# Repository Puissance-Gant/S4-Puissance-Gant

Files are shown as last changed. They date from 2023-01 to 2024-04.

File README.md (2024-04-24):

# S4-Puissance-Gant

Voici le répertoire du projet de session de l'équipe Puissance Gant :gloves::robot:

## Membres
<pre>
- Comtois, Ludovic    (coml1502)
- Corduneanu, Andrei  (cora5428)
- Delev, Milan        (delm1301)
- Den Hartog, Daniel  (deno2501)
- Martin, Frédérick   (marf0702)
- Theoret, Marek      (them0901)
</pre>

## Objectif du projet
L'équipe Puissance Gant avait pour but de concevoir une main robotisée ainsi qu'un système de contrôle à distance intuitif. Le produit final consiste en une main à trois doigts indépendemment contrôlés par un gant auquel des potentiomètres coulissants ont été attaché. Une interface utilisateur permet d'observer l'état du robot et de le contrôler manuellement.

### Le projet en action
cliquez sur l'image:<br><br>
[](https://youtu.be/RtNsFn4x6qA)

## Fonctionnement global
Le fonctionnement spécifique de chaque composante est décrite dans leur sous-dossier respectif.

Il y a trois composantes principales qui communiquent entre elles à l'aide d'un serveur de communication sans-fil par WI-FI. L'état du gant est lu par une carte ESP32 qui envoie la position des doigts au système. Un ordinateur reçoit ces informations et les transmet à une carte OpenCR qui contrôle les moteurs de la main. Un deuxième ordinateur affiche une interface utilisateur qui permet d'afficher des informations utiles et de contrôler la main manuellement.

### Performance
La latence globale du contrôle, donc entre le mouvement de la main de l'utilisateur et le mouvement de la main est d'environ 200ms et est plutôt constant. La main peut d'ailleurs tenir une banane de 200g sans la faire tomber.

### Pistes d'amélioration
<pre>
- Changer la forme de la main robotisée et l'emplacement des doigts afin d'optimiser la prise d'objets. 
- Utiliser un meilleur système de tension pour la prise d'objets, qui empêcherait les doigts de bouger lors de la prise d'objets.
- Changer la carte OpenCR pour une carte qui peut se connecter au WI-FI. (Par exemple, un ESP32 et une carte-soeur de contrôle des moteurs)
- Rendre le serveur accessible sur tous les réseaux. Les appareils doivent actuellement être sur le même réseau WI-FI que le serveur pour s'y connecter.
- Changer le système d'acquisition de données du gant. Par exemple, un exosquelette. (Faire attention aux résistances flexibles, elles sont souvent peu fiables.)
</pre>

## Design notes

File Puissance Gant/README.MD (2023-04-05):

# Organisation des dossiers
Les dossiers sont organisés tel que l'assemblage physique de la main et du gant sont dans un dossier séparé de la programmation qui leur est associé.

Les sous-dossiers de programmation indiquent comment utiliser le code, quelles librairies installer et sur quel appareil installer quel code.

Les sous-dossiers de mécanique et d'électrique indiquent comment assembler le gant et la main et quel matériel a été utilisé.

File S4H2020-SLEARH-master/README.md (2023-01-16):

# Project-SLIRUS
Articulated robotic hand designed for sign language interpretation
Continuation from the SLEARH project: https://github.com/UdeS-GRO/S4H2020-SLEARH

# Preriquisites:
Hardware:
  - Open CR;
  - 1 usb to micro usb;
  - 1 drive for the motors ( (PCA-96 85) link: https://www.sunfounder.com/pca9685-16-channel-12-bit-pwm-servo-driver.html);
  - 12 electrical step motors ((Smraza 9G Micro Servo Motor) link: https://www.amazon.ca/gp/product/B0886351PP/ref=ppx_yo_dt_b_asin_title_o00_s00?ie=UTF8&psc=1);
  - RaspberryPi 3B+;
  - Micro-SD card (for RPi image);
  - 2 Dynamixel XL-430;
  - A voltage source with a current limit of more than 2 A;
  - 12 V power source, to 5.1mm center positive barrel jack;
  - Piece of plywood 30cm by 30cm (optional, but recommended);
  
Software;
  - Python 3.7(installed for this gitProject, but not necessarily needed);
  - Python Library:
    - pySerial;
    - tkinter;
  - Arduino IDE for the compiler;
  - Arduino Library:
    - Adafruit_PWMServoDriver.h;
    - ArduinoJson.h;
    - Wire.h;
    (But they all should be downloaded with the plateformio.ini)
  -Qt (5.7.1 or newer)
    
# Steps to start your project:
  - Read the Mechanics/README.md for informations on how to build the hand;
  - Read the Electrics/README.md for informations on how to plug the motors and the drive on the arduino;
  - Read the Interface/README.md for informations on how to use the interface
  - Read the Speech_to_text/README.md for informations on how to install the necessary librairies for the speech-to-text and create a key for the API connection
  - Install your favorite python IDE;
  - Open this git repo in a new project and create a python RunTool for UI_Main_Script.py script (that's where the application starts);
  - Install pySerial on your computer (it will appears in your python <python path>/Lib/*);
  (Now, your python side of the project should be up to run)
  - Install VsCode on your computer;
  - Install plateformio and ArduinoIDE in your vscode;
  - Set your Arduino_debug.exe path in your VsCode setups;
  - Build the project one first time (and it should load all the needed libraries);
  (Now, your Arduino side of the project should be up to run)
  - Import OpenCr library as shown in this video: https://www.youtube.com/watch?v=dQw4w9WgXcQ
  - Plug the Arduino to your computer and start the UI_Main_Script.py to start the application and the Arduino thread!
  
 # Steps to be able to run to application on the Raspberry Pi 3b+
  - Flash your Micro-SD card with an up to date RPi image running a linux operating system (you can flash your Micro-SD card with this       tool: https://www.balena.io/etcher/);
  - Connect your Micro-SD card in your RPi and open it with an internet cable or via VMWare for example;
  - On the first RPi's run, set your preferences;
  - Now, open a terminal and instal python 3.6 (or niewer, this could take some time) (this link could be usefull: https://github.com/instabot-py/instabot.py/wiki/Installing-Python-3.7-on-Raspberry-Pi);
  - Install the PySerial library with:
    $ sudo apt-get install pyserial
  - If you're connected to your RPi via VMWare or ssh, run this command:
    - $ export DISPLAY=:0
  - Create your project directory where you want it on your RPi:
    - $ cd "DIRECTORY PATH"
    - $ mkdir "PROJECT NAME"
    - $ cd "PROJECT NAME"
    - $ git clone "THE PROJECT'S LINK"
    - $ git pull
  - The project should now be copied locally onto your RPi;
  
  - Now go to the project's Ui_Main_script.py path on your RPi and run the program through a terminal:
    - $ python Ui_Main_Script.py
  
# Now Have Fun !

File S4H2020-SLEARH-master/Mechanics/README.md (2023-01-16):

ASSEMBLY OF THE HAND

1. Start by opening the BOM file in this folder.
2. With a 3D printer at 40% fill and supports, print all the parts that have &quot;3D printed&quot; as a link. Some parts need to be printed more than once, refer to the quantity column of the BOM to know how many.
3. Cut all the pivot rods with lenghts and quantity as described in the BOM (index 15-16)
4. Separate all the printed parts for each of the fingers where each number is the index in the BOM;

Pinky: 2 – 6 – 4 – 5

Ring finger: 2 – 6 – 4 – 5

Middle finger: 1 – 6 – 4 – 5

Index finger: 1 – 6 – 4 – 5 - 13 - 10 - 18

Thumb: 3 – 6 – 8 – 10 – 9 - 12

The assembly of the fingers is done with rods that are used as pivots in the joints. The servos' moving lever are fixed on the 3D printed levers with nails. The nail's head holds the lever in place and the other end is press fitted into the 3d printed lever.

Assembly of the pinky finger:
1. Attach part 2 and 6 with a 14mm pin. The assembly should be able to move freely.
2. Attach part 2 and 4 together with a 14mm pin.
3. Screw a Servo on part 6.
4. Attach part 5 and 6 with a 14mm pin.
5. With a nail, attach part 4 to the servo screwed on part 6.
6. Screw a servo on part 7.
7. With a nail, attach part 5 to the servo screwed on part 7.

For the four other fingers follow the same steps as for the pinky finger using the parts specified earlier.

When the fingers are assembled, the servo holders are cliped on the palm and a rod is inserted in the pivot.

Assembly of the base:
8. Install the motors drive on the back of the hand with the four bolts of index 29.
9. Make all the electric connections relating to the hand motors as explained in the electric README.
10. Insert a rod of index 26 into the forearm (index 20) until the exposed part of the rod is roughly the same length as the thickness of the base.
11. With the bolts of index 28, install the Open CR and the raspberry pi on the forearm.
12. Insert one of the Dynamixel in the cage located on the forearm until the rotating circle is level with the exterior of the cage.
13. Fasten the 3D printed piece of index 23 to the Dynamixel installed in step 24 using 2 bolts of index 27.
14. Insert the other Dynamixel in the rectangular enclosure in the base, and fasten the gear of index 21 to said Dynamixel using 2 bolts of index 27.
15. Insert 2 bearings of index 22 in the circular grooves in the base.
16. Place the protruding rod of the forearm into the hols in the base, making sure that the gear installed in step 26 and the gear of the forearm mesh together.
17. Connect the hand to the forearm using a rod of index 25, making sure that the driver side of the palm faces the Dynamixel in the forearm.
18. Install the wrist lever arm (index 24) between the forearm dynamixel and the protruding hole at the bottom of the palm.
19. Connect the Dynamixels as explained in the electric README.
If desired, you can screw a wooden platform to the base for added stability.

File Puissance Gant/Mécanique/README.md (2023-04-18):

# GUIDE D'ASSEMBLAGE DE LA MAIN ET DE L'AVANT BRAS

1. La main est une pièce unique fait a l'aide de solidworks, comme toutes les autres.



2. Afin de joindre les 14 pièces différentes, bien identifié dans le dossier, qui servent de doigts, il faut prendre un élastique coupé et le mettre de manière à ce que chaque bout de l'élastique passe dans un des deux trous arrières de la pièce. Une fois les trois pièces de doigts assemblées (deux pour le pouce) il faut passer l'élastique dans les deux trous arrière du haut de la main prévu pour chaque doigt. (1 à 2 élastiques par doigts) 




3. Avant d'attacher l'élastique il faut que celui-ci soit tendu le plus possible sans qu'il ne fend.

4. Deux vis(Ø~0.5cm,longueur>3.5cm), quatres rondelles et deux écrous permettent de connecter la main et l'avant-bras

5. Les trois moteurs ROBOTIS Dynamixel X-Series XL430-W250 sont placés à l'avant de l'avant-bras en positionnant le rotor de chaque moteur coïncidement avec les extrusions dans l'avant-bras prévu à cet effet. Ces moteurs sont fixés à l'avant-bras à l'aide de 8 vis pour chacun des moteurs. Les vis sont celles fournies dans le kit des moteurs.

6. Une poulie est fixé sur chacun de ces moteurs à l'aide de 2 vis, celles du kit. Un fil de pêche est attaché sur chacune des poulies en le passant tout d'abord par le trou au milieu des poulies les traversant. Cela permet de s'assurer que le noeud sur la poulie ne bougera pas. Ensuite, passer le fil dans les trous avant repectifs de l'avant-bras et de la main puis ensuite des doigts (pas le majeur et le petit doigts), jusqu'à le joindre au bout de chaque doigt à l'aide de l'élastique.



8. Le majeur, l'annulaire et le petit doigt sont relié entre eux par des bouts de bois collés avec de la colle chaude sur le derrière des phalanges. (2 morceaux, 1 en bas / 1 en haut, sur la phalanges du bas et 1 morceaux au milieu des deux autres phalanges)

9. Le moteur ROBOTIS Dynamixel X-Series XM430-W350 est installé sur l'arrière de l'avant-bras de la même manière que les trois XL430.

10. La pièce Mécanisme_Poignet_1 est attaché sur le moteur XM430 de la même manière que les poulies sur les autres moteurs.

11. La pièce Mécanisme_Poignet_2 est collé au milieu du derrière de la main ainsi qu'au Mécanisme_Poignet_1 avec de la colle chaude.

# Amélioration possible 

1. L'avant bras pourrait permettre d'accueillir deux moteurs de plus afin de contrôler individuellement chaque doigt.

2. Le pouce pourrait avoir une troisième phalanges et être repositionné pour lui permettre un mouvement plus utile lors de la prise d'objet.

3. La main pourrait être fait de manière plus concave afin de mieux reproduire sa forme réelle.

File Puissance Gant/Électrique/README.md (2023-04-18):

### Mécanique du gant
diag_mec

Description du montage:
- Chaque curseur de potentiomètre est attaché à un ressort le retenant à sa position zéro, soit vers l'arrière (vers le poignet).
- Chaque curseur est ensuite tiré par un câble, chacun parcourant au moins trois corridors d'alignement:
  - Au moins un corridor est placé sur le boitier, servant de premier point d'appui au câble pour ensuite se diriger vers le doigt assigné.
  - Au moins deux corridors sont placés sur chacun des doigts à mesurer et chacun est fixé sur un bague que l'utilisateur doit porter.
  - Les corridors sur les bagues distales servent de point d'ancrage au câble.
  - Plus de corridors peuvent être installés afin de maximiser la linéarité de la translation axiale du câble.
- En fléchissant les doigts, le câble est tiré, faisant varier la position du curseur du potentiomètre.
- Les ressorts doivent être suffisamment forts pour retenir les doigts au repos en position ouverte.

### Électronique du gant
diag_elec

Description du montage:
La mesure de la position des doigts se fait par la lecture des diviseurs de tension de chaque doigt
- Une résistance fixe est placée en série à un potentiomètre. Ici, 10 k et 100 k ohms respectivement.
- On applique la tension (Vcc; 3,3 V) à la résistance fixe et on branche le point du curseur à la masse (GND)
- La borne extrême du potentiomètre (résistance totale fixe) peut ne pas être branchée, cependant:
  - En fonction du modèle de potentiomètre, il est possible de placer la résistance fixe entre les bornes non-variables pour concevoir le diviseur de  tension, rendant le montage plus compact.
  - Dans le cas décrit ci-haut, la résistance fixe doit être de 11k afin d'équivaloir, avec la 100 k du potentiomètre, à 10 k ohms (circuit parallèle).
- La borne Vout (point de lecture) est entre la résistance fixe et le potentiomètre.
- La borne Vout de chaque diviseur de tension est branchée directement en input au ESP32D aux points GPIO 36, 39 et 34 pour le pouce, l'index et le majeur respectivement.
- Les points du ESP32D peuvent varier en fonction de votre programme.

### Photos de montage complété
Bien que rudimentaire, le montage illustré ci-contre sert de référence pour l'assemblage. À noter que les tiges des curseurs traversent le plafond du boitier dans une fente de la langueur du parcours du curseur et que les poteniomètres sont boulonnés par le haut.
gant_montage02

gant_montage01

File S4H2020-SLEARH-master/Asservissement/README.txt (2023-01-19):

Motors control

This README will explain how to control the different motors on the hand.
In the document Test_main, you can find all the three files needed for the motor control.

Test_main.ino
•	This file is the main. 
•	This is where we initialize all the motors (servomotors and dynamixels). When started, the hand stands up at is initial position and wait for a message from the interface.
•	The main uses the class COM_Arduino in the file Communication.h for all the function connected to the communication with the interface.
•	When a message is received from the interface, the functions from class Servo of the file controlServo.h are called to execute a letter.

controlServo.h
•	This file contains the class Servo.
•	The class Servo contains the struct Servo and all the function used in for the control of the motors.
•	The struct Servo contains all the configurations of the 5 fingers, the wrist and the base for all the characters (letters and numbers).
•	The three functions called form the main (Test_main.ino) are the setupBase, servoOut and the reverseMove.
•	The function setupBase is used to move the base and wrist at its initial position depended on is initial position.
•	The function servoOut is use the move all motors in the configuration of a specific letter or number.
•	The function reverseMove is use to replace the hand in is initial position.

Communication.h
•	This file contains the class COM_Arduino.
•	The class COM_Arduino contains all the function use to communicate with the interface.
•	The functions SendMessage and ReadMessage interact with the interface.
•	The functions Set_state and Get_state are useful if you want to manage the state of the object.

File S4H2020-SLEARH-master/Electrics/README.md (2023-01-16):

# Electrical Parts list

    Name	              Description	                                Quantity
    ------------------------------------------------------------------------
    Open CR     	      OpenCR1.0     	                              1
    Servo driver	      PCA9685 16 channel PWM servo Driver	         1
    Servo motors	      SG90 servo motor	                              12

# Electrical Connections:

  # OpenCR pins to Drive Pins
    - 5V   ------->    VCC
    - Ground  ---->    Ground
    - scl(pin15) ->    scl
    - sda(pin14) ->    sda
    
  # Drive pins to Servo Motors    
    - 0      --------> motor 0 (thumb bottom)
    - 1      --------> motor 1 (thumb top)
    - 2      --------> motor 2 (index bottom)
    - 3      --------> motor 3 (index top)
    - 4      --------> motor 4 (middle bottom)
    - 5      --------> motor 5 (middle top)
    - 6      --------> motor 6 (ring bottom)
    - 7      --------> motor 7 (ring top)
    - 8      --------> motor 8 (pinky bottom)
    - 9      --------> motor 9 (pinky top)
    - 10     --------> motor 10 (index base) 
    - 13     --------> motor 11 (thumb base) 

The 2A voltage source must be connected to the 2 pin terminal block of the drive.
The voltage source with the barrel jack must be connected to the female adapter on the OpenCR.
The 2 Dynamixel servos can be plugged into any of the TTL ports on the OpenCR.

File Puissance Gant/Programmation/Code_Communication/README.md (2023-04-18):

# Architecture de la communication
Le projet Puissance Gant utilise les protocoles MQTT et sériel pour faire communiquer les divers éléments. Le schéma suivant illustre les divers liens entre les contrôleurs et ordinateurs ainsi que les protocoles utilisés.
architecture_comm_2 drawio

# Communication sans-fil par MQTT
Cette section contient le processus pour l'installation et la configuration d'un serveur MQTT. MQTT est un protocole de communication sans fil utilisé dans les situation oû la bande passante est peu fiable ou faible. Le protocole MQTT utilisé est Eclipse Mosquitto. Il recommender d'installer le mqtt explorer afin de vérifier l'état du serveur. 

http://mqtt-explorer.com/

## Installation du serveur sur le raspberry pi

Afin d'installer le serveur sur le raspberry pi, il faut tout d'abord intaller un système d'operation. Le système d'operation recommandé est ubuntu server 22.10. 

https://ubuntu.com/download/server

Par la suite, il faut installer un serveur MQTT sur le raspberry pi. Pour l'installation, il est recommendé de suivre le tutoriel suivant: 

https://diyi0t.com/microcontroller-to-raspberry-pi-wifi-mqtt-communication/

Il d'ailleurs utile d'installer *MQTT Explorer*, qui est une application qui permet de visualiser et de gérer les messages en temps réel. Celà facilite le débogage et le développement d'applications MQTT.

http://mqtt-explorer.com/

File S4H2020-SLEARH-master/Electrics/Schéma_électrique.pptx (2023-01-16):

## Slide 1

PCA9685
16 CHANNEL 12-BIT PWM
I2C ADDRESS I[A5..A0][R/W]
VDD : 2.3-5.5V IO : 5V SAFE
OUTPUT : 25mA EACH/400mA TOTAL

GND PWM0
SDA PWM1
SCL PWM2
VCC PWM3
PWM4
PWM5
PWM6
PWM7
PWM8
PWM9
PWM10
PWM11
PWM12
PWM13
PWM14
PWM15

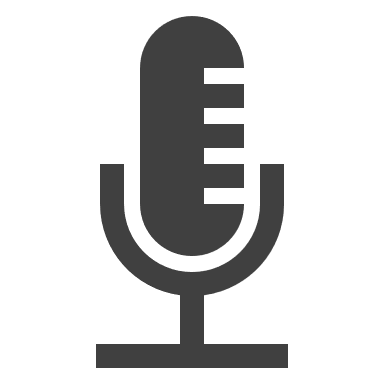
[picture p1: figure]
Micro de radio avec un remplissage uni

RASPBERRY PI

USB
USB
MICRO USB

OPENCR

GND
MICRO USB SDA
SCL
5V

POWER
SMPS IN

SERVO SG90-1
SERVO SG90-2
SERVO SG90-3
SERVO SG90-4
SERVO SG90-5
SERVO SG90-6
SERVO SG90-7
SERVO SG90-8
SERVO SG90-9
SERVO SG90-10
SERVO SG90-11
SERVO SG90-12

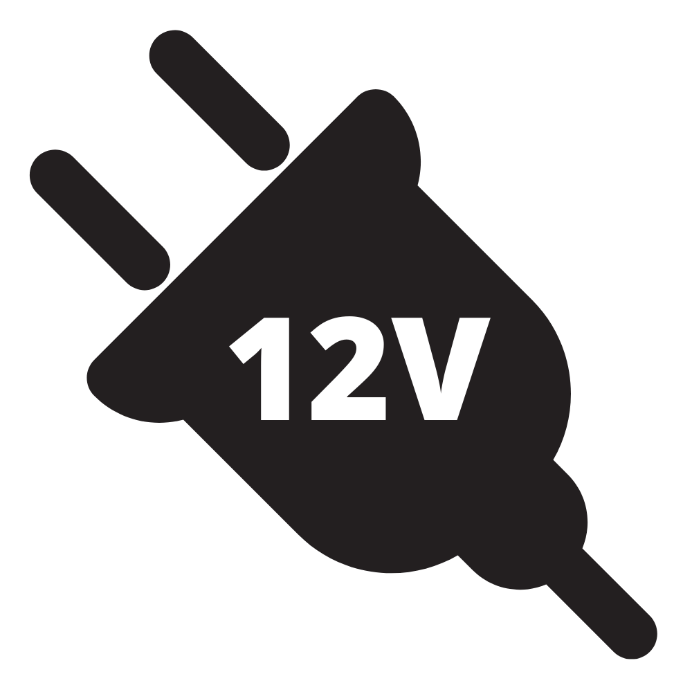
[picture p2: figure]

5V

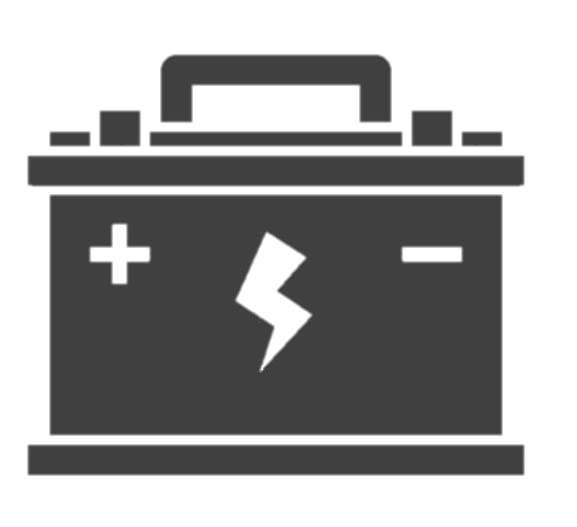
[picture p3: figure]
Car battery icon | Battery icon, Car battery, Car battery hacks

5V

AUXILIARY POWER
V+
GND

GND EXTCLK WHEN NOT IN USE

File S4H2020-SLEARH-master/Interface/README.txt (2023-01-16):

User interface:

The software used for the user interface was Qt 5.10. Be sure it is already installed before beginning the project
The program is ready to be used directly when you open it. However, some paths to other files (Enregistrement.py and 
FinPort.py) are implemented for our project. Make sure that these paths are modified for your files.
Furthermore, some aspects of the insterface can be used without the OpenCr (Speech-to-text and show characters), but the
transcription need the OpenCr to work well. 

Interface properties:
-The line edit on the top left changes the recording time of the speech-to-text. A recording time negative or 0 will trigger
an error message. Decimals have not been managed. The program only works if an integer is written. 
-The "Start record button" creates a process that runs the Enregistrement.py file. A label will appear when the program is ready 
to receive sound. Another label will appear when the recording is finished.
-After recording your phrase, it will appear underneath the Recording button.
-On the bottom left is the Start traduction button. It can only be used if a phrase has been recorded with the Speech-to-text property.
-On the bottom right, you can write a character to see the sign assciated with it. You can also write "all" to see every character
at the same time.
-On the top right, the big blank space will show the images of the characters.
-The last line edit on the bottom right near the middle is used for tests. You can write one or multiple characters and press enter 
to start the hand traduction. This way, you don't need to use the speech-to-text if you only want to test on or few letters.

When the traduction is started, the hand will show every character one by one. At the same time, the interface will show the character
the hand is doing. 

FindPort:
Communication between interface and OpenCr.

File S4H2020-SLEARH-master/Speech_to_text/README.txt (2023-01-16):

%%%%% This file will explain how to run the speech-to-text API on a Raspberry pi 3b+
 %%%%%

1. Creat_VenV.py

If you want to run you program in a virtual environment, you`ll need to create one. 
This file lets you chose the path and the name of your virtual environment.
ATTENTION: This file will not work on Windows or Mac, because the file writes directly in the command window available only in Linux

It is recommended to create a virtual environment if you have multiple python programs and they use different versions of modules/Packages. By creating a virtual environment, you can isolate the necessary 
packages and run them with the right program. An old library version is used in this folder, so a virtual envrionment may be helpful.

2. Install librairies

Libraries installations are quite simple with the right tools. First of all, be sure to install pip on your Raspberry pi

2.1  Activate virtual environment

If you have decided to create a virtual environment, you need to activate it to install the required packages

	2.1.1 - Open the command window (Habitually a black box on the top left)
	2.1.2 - write: "source /path/to/venv/bin/activate"
	2.1.3 - The virtual environment name should be written in the command window

You are now ready to install libraries in the virtual environment

2.2 Install librairies for the project

	2.2.1 - Open the command window
	2.2.2 - Write "python3 -m pip install package" where the "package" in the project is: soundfile, sounddevice, google-cloud-storage and google-cloud-speech

ATTENTION: We used the version 2.0.0 for the google-cloud-speech library. The RecognitionAudio and RecognitionConfig have then been modified

	2.2.3 - With these packages, the program may not work. At the moment of the project's creation, there are numpy and PortAudio problems with sounddevice and the Raspberry pi OS. 
	   You will then need to install a few more packages if it is your case.
	   Open the command window and write: "sudo apt-get install " and then install these libraries: libportaudio2, libasound-dev and libatlas-base-dev

3. Connection to API

In the file Enregistrement.py, a key is necessary to be able to use the Speech-to-text API.
When you create your own google-cloud account, you need to be able to get the key.
The key should be a json file and must be in the same folder as Enregsitrement.py when it is running or you need to write the full path to the key.

Step by step on how to setup the google cloud project for SLIRUS:
3.1-Create a google cloud project:
	3.1.1 - Create a google account(gmail) if you don't already have one. Be sure to put in a billing methode with the account. 
	3.1.2 - Go to the url--> https://console.cloud.google.com/
	3.1.3 - Click on the 3 dash bars on the top left of the screen.
	3.1.4 - Put your mouse on "Home" and click on "Dashboard".
	3.1.5 - Click on "New projet" and fillout the missing information.
3.2-Enable the Speech to text API for the project:
	3.2.1 - Click on the 3 dash bars on the top left of the screen.
	3.2.2 - Click on "APIs & Services".
	3.2.3 - Click on "ENABLE APIS AND SERVICES" at the top of the page.
	3.2.4 - Put "Cloud Speech-to-Text API" in the search bar and press Enter.
	3.2.5 - Click on the API "Cloud Speech-to-Text API".
	3.2.6 - Click on "ENABLE".
3.3-Get your JSON key:
	3.3.1 - Go back to "APIs & Services" and click on "Credentials".
	3.3.2 - Click on "Create Credential" and choose "Servive account".
	3.3.3 - In the menu click on "IAM & Admin" then on "Service Accounts".
	3.3.4 - Click on your service account and go to "KEYS".
	3.3.5 - Click on "ADD KEY" and choose JSON.

Now you should have the JSON key downloaded. This will allow you to have access to the APIs that were enable for your projet. 

4. Create a bucket in your google cloud project:
	4.1-Click on "Storage" in the menu. 
	4.2-Click on "CREATE BUCKET" and fill in the information required.
Remember the name of your bucket because you'll need to put it in the code ...

5. Run Enregistrement.py in the virtual environment

This section is reserved to those who use a virtual environment. 
To open the file in the virtual environment (and use the libraries inside), be sure that the virtual environment is still active.
Then, write in the command window "cd /path/to/file"
You should now be in the folder with the right files
Write in the command window "python3 Enregistrement.py" 
  
You should now be able to transcribe your voice into text.

6. Run Enregistrement_automatic_tests
This program lets you test your speech-to-text
Some words/sentences are already written in french. If you want to test in another language, you juste need to change them for what you want.
The recording time is set to 5 sec, but you can change it to whatever you want in the line calling the function
To make it work, speak clearly and a constant pace. 
Don't try too difficult phrases, because the API sometimes does little ortograph mistakes (For example "it eat")

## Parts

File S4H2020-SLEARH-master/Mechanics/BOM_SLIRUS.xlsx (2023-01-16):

Index | Part name | Qty | 3DPrinted | Description
1 | Phalange_Index-MiddleFinger | 2 | x | Index and middle finger end
2 | Phalange_RingFinger-PinkyFinger | 2 | x | Ring and Pinky finger end
3 | Phalange_thumb | 1 | x | Thumb finger end
4 | Finger_lever_distal | 4 | x | Lever for the four finger ends (except thumb)
5 | finger_lever_proximal | 4 | x | Finger lever that links fingers to the palm
6 | SG-90 Servo Socket | 5 | x | Servo Holder (part of the fingers)
7 | Servo Holder | 4 | x | Fix servo on the palm
8 | Thumb_Finger_lever_distal | 1 | x | Finger lever to move thumb end
9 | Proximal_thumb_lever | 1 | x | Lever to move thumb second part
10 | SG90 - Servo Socket_thumb | 1 | x | Servo socket (part ofthe thumb)
11 | Servo_holder_index | 1 | x | Holds servo on the index
12 | Thumb_lever | 1 | x | Lever for the whole thumb
13 | Palm_index | 1 | x | Part of the palm for index movement
14 | Palm | 1 | x | Palm
15 | 14mm pivot rod | 21 |  | 2mm x 14mm
16 | 17mm pivot rod | 2 |  | 2mm x 17mm
17 | SG90 micro servo | 12 |  | Servos to move the fingers
18 | palm_index_lever | 1 | x | Moves the index finger assembly
19 | Base | 1 | x | Allows rotation of the arm
20 | Arm | 1 | x | Forearm of the hand
21 | Gear | 1 | x | Rotates in order to rotate arm
22 | Flanged Ball Bearing | 2 |  | 1/4" ID x 1/2" OD
23 | Dynamixel_Coupler | 1 | x | Connects Dynamixel servo to lever arm
24 | Wrist_lever | 1 | x | Allows rotation of the wrist
25 | 1/4" x 4" D-shaft | 1 |  | Pivot for the wrist
26 | 1/4" x 8" D-shaft | 1 |  | Connects arm to base and allows rotation
27 | M2.0 bolt | 4 |  | Used to fix pieces to dynamixel
28 | M3-0.5 | 4 |  | Used to fasten open CR to Arm
29 | M2.5-0.45 | 4 |  | Used to fasten drive to hand

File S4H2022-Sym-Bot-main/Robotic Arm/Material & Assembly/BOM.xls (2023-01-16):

ITEM NO. | PART NUMBER | DESCRIPTION | QTY.
1 | Base | 3D printed | 1
2 | Holding_Ring | 3D printed | 1
3 | Arm_base | 3D printed | 1
4 | Rotation_Gear | 3D printed | 1
5 | Gear_Shaft | 3D printed | 1
6 | Coupler Medium | 3D printed | 1
7 | Coupler350W | 3D printed | 2
8 | M3 brass insert |  | 6
9 | M6 brass insert |  | 4
10 | 545548_hub | Kit Actobotics | 6
11 | 5-16_Stainless_Steel_Ball |  | 49
12 | XL430-W250 | Dynamixel motor | 1
13 | XM430-W350 | Dynamixel motor | 2
14 | Arm_1A | 3D printed | 1
15 | Arm_1B | 3D printed | 1
16 | Arm_2 | 3D printed | 1
17 | shaft | 1/8" 3" long D shaft | 2
18 | base_1 | 3D printed | 1
19 | base_2 | 3D printed | 1
20 | claw_rack | 3D printed | 2
21 | claw_tip | 3D printed | 2
22 | driving_gear | 3D printed | 1
23 | adaptor | 3D printed | 1
24 | #6 Nylon washer | Kit Actobotics | 8
25 | 1/4" Spacer | Kit Actobotics | 4
26 | hs-422 | Hitec 180 degree servomotor | 1
27 | horn cross | Hitec cross-shaped adaptor | 1
28 | M3 10mm screw | M3 10mm cone head screw | 6
29 | M3 10mm screw | M3 10mm socket head screw | 4
30 | M3 20mm screw | M3 20mm socket head screw | 4
31 | M3 hex nut | M3 screw hexagonal nut | 8
32 | 6-32 3/4" screw | 3/4” x 6-32 Zinc-Plated Socket Head Screw | 14
33 | 6-32 1/2" screw | 1/2” x 6-32 Zinc-Plated Socket Head Screw | 1
34 | 6-32 3/8" screw | 3/8” x 6-32 Zinc-Plated Socket Head Screw | 8
35 | 6-32 1/4" screw | 1/4” x 6-32 Zinc-Plated Socket Head Screw | 1
36 | 6-32 hex nut | 6-32 screw hexagonal nut | 14
37 | 585474 screw plate | 6-32 screw square nut | 2

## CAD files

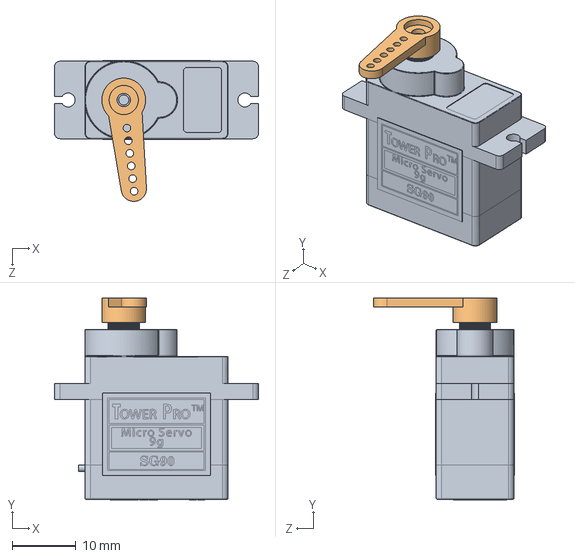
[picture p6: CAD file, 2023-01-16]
S4H2020-SLEARH-master/Mechanics/CAD/SG90 - Micro Servo Assembly.SLDASM
32.1 x 31.8 x 22.2 mm
SG90 - Micro Servo 9g - Tower Pro.1
SG90 - Micro Servo 9g - Tower Pro.2

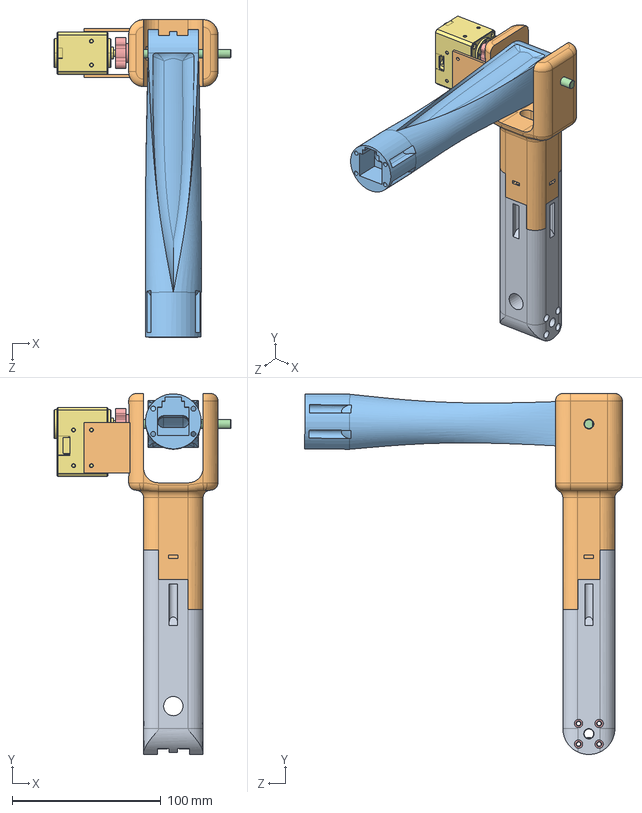
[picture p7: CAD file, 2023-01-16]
S4H2022-Sym-Bot-main/Robotic Arm/Material & Assembly/Arm/Arm.SLDASM
118.6 x 242.5 x 213.5 mm
Arm_1A
Arm_1B
Arm_2
shaft
545548.STEP x 5
632138_91375A438.STEP x 5
XM430-W350

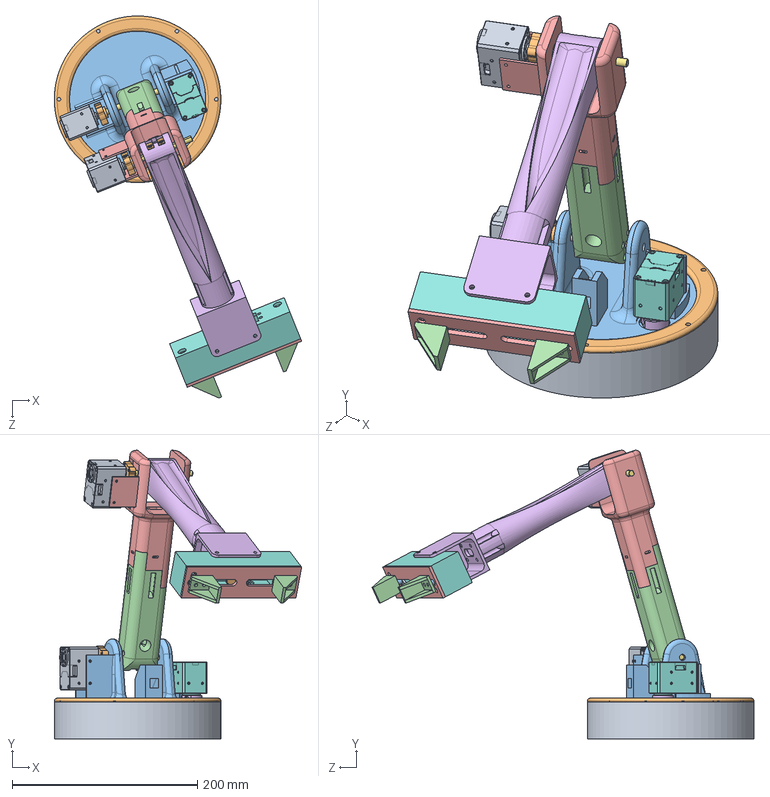
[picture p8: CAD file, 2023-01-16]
S4H2022-Sym-Bot-main/Robotic Arm/Material & Assembly/Sym-Bot.SLDASM
267.3 x 311.9 x 412.8 mm
Base
Holding_Ring
Arm_Base
Rotation_Gear
5-16_Stainless_Steel_Ball x 49
Coupler_Medium
Gear_Shaft
XL430-W250
XM430-W350 x 2
545548.STEP x 6
632138_91375A438.STEP x 6
Arm_1A
Arm_1B
Arm_2
shaft x 2
base_1
claw_rack x 2
driving_gear
spacer x 4
claw_tip x 2
base_2
adaptor
washer x 8

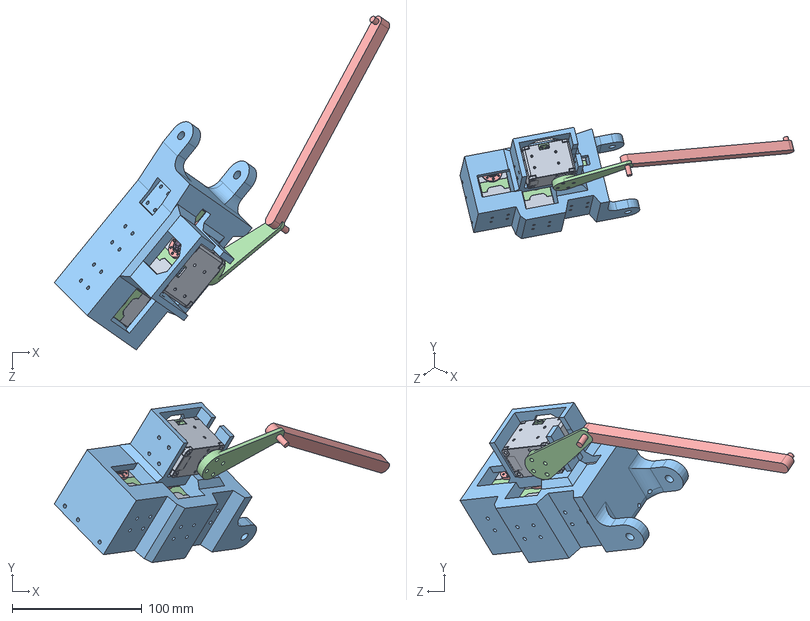
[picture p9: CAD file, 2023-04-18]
Puissance Gant/Mécanique/Assemblage Avant bras.SLDASM
258.2 x 123.3 x 257.0 mm
DC11_A01_DUMMY.stp x 4
DX124_SCREW-COVER.stp x 4
B3B-EH.stp x 8
DC11_A01_CASE_CVR_DUMMY.stp x 4
DC11_A01_IDLER_DUMMY.stp x 4
DC11_A01_IDLER_CAP_DUMMY.stp x 4
DC11_A01_IDLER_SCREW.stp x 4
FHS_M2_5X10.stp x 32
DC11_A01_SPACER_DUMMY.stp x 32
Poulie v2 - Copy x 3
FOREARM1 - Copy
Mécanisme poignet 1
Mécanisme poignet 2

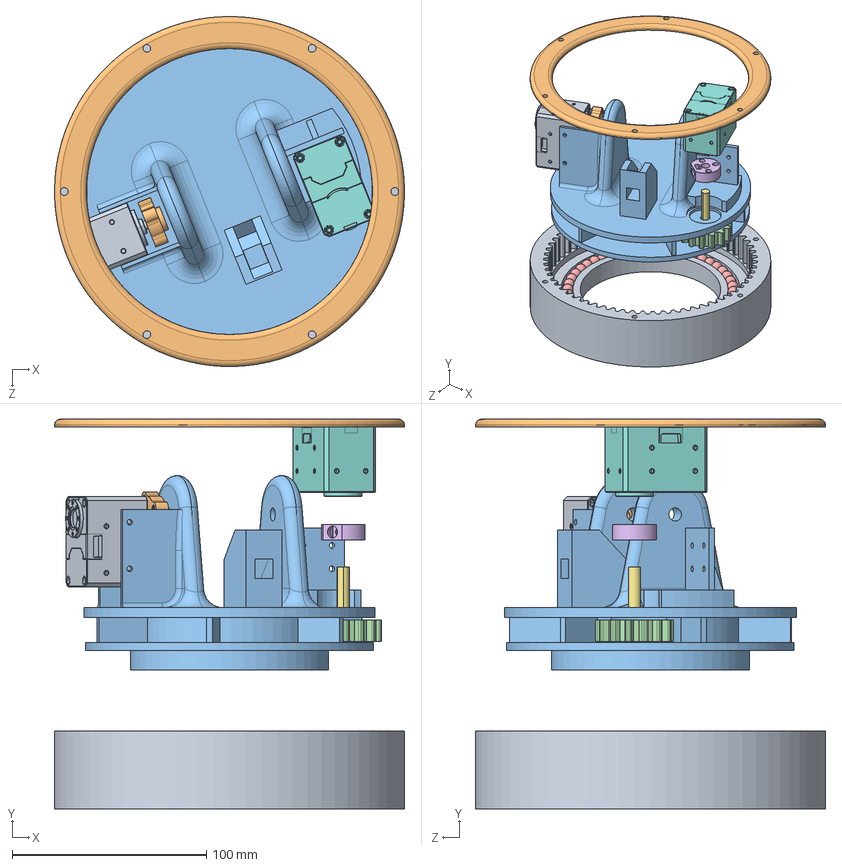
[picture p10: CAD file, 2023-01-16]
S4H2022-Sym-Bot-main/Robotic Arm/Material & Assembly/Base/Base.SLDASM
180.0 x 200.4 x 180.0 mm
Base
Holding_Ring
Arm_Base
Rotation_Gear
5-16_Stainless_Steel_Ball x 49
Coupler_Medium
Gear_Shaft
XL430-W250
XM430-W350
545548.STEP
632138_91375A438.STEP

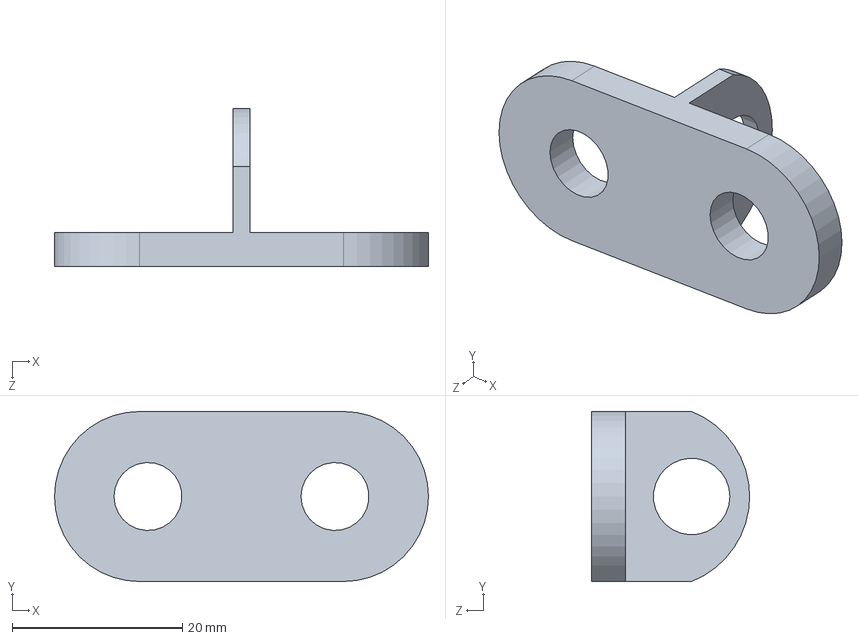
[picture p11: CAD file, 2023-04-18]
Puissance Gant/Mécanique/support main vers mecanisme.SLDPRT
44.0 x 20.0 x 18.6 mm

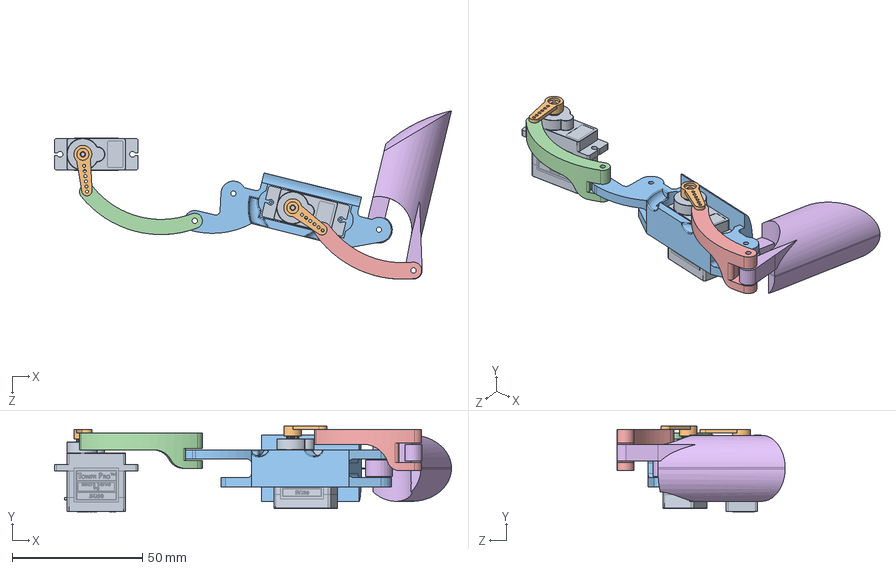
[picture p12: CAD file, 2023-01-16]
S4H2020-SLEARH-master/Mechanics/CAD/Ring_PinkyFinger.SLDASM
152.6 x 33.0 x 64.7 mm
SG90 - Micro Servo 9g - Tower Pro.1 x 2
SG90 - Micro Servo 9g - Tower Pro.2 x 2
SG90 - Servo Socket
finger_lever_proximal
Finger_lever_distal
phalange_RingFinger-PinkyFinger

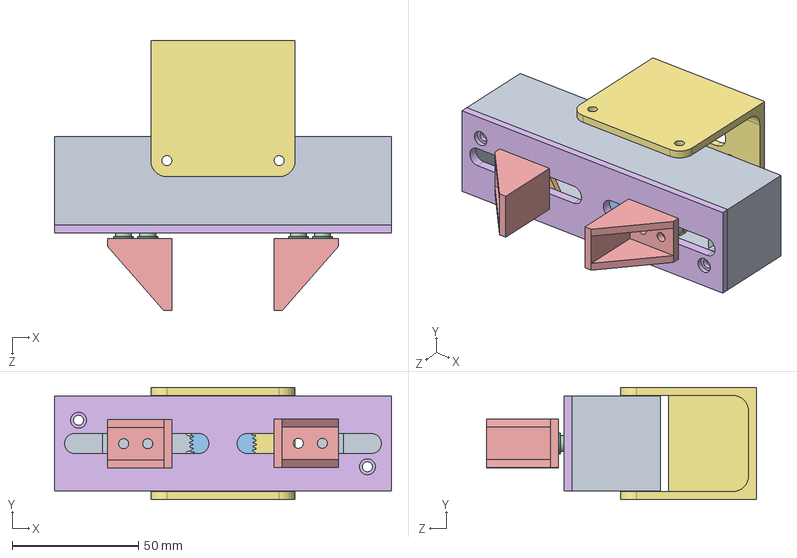
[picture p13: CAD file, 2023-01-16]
S4H2022-Sym-Bot-main/Robotic Arm/Material & Assembly/Gripper/gripper_assy.SLDASM
133.4 x 44.5 x 107.0 mm
base_1
claw_rack x 2
driving_gear
spacer x 4
claw_tip x 2
base_2
adaptor
washer x 8

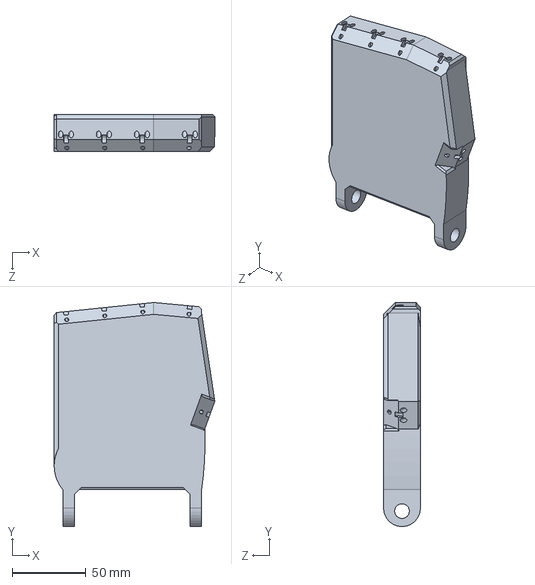
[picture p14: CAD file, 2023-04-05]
Puissance Gant/Mécanique/main.sldprt
109.0 x 151.9 x 25.0 mm

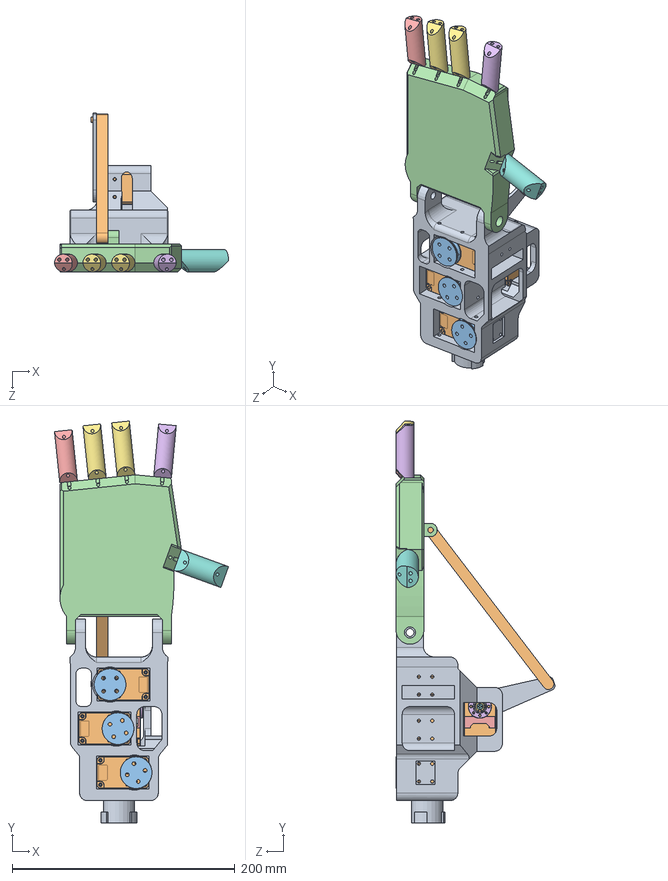
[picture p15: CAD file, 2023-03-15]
Puissance Gant/Mécanique/Assemblage_total.sldasm
156.3 x 360.9 x 142.6 mm
FOREARM1
DC11_A01_DUMMY.stp x 4
DX124_SCREW-COVER.stp x 4
B3B-EH.stp x 8
DC11_A01_CASE_CVR_DUMMY.stp x 4
DC11_A01_IDLER_DUMMY.stp x 4
DC11_A01_IDLER_CAP_DUMMY.stp x 4
DC11_A01_IDLER_SCREW.stp x 4
FHS_M2_5X10.stp x 32
DC11_A01_SPACER_DUMMY.stp x 32
Poulie x 3
main
bas petit doigt
bas annulaire+index doigt
bas majeur doigt x 2
bas pouce
Mécanisme poignet 1
Mécanisme poignet 2

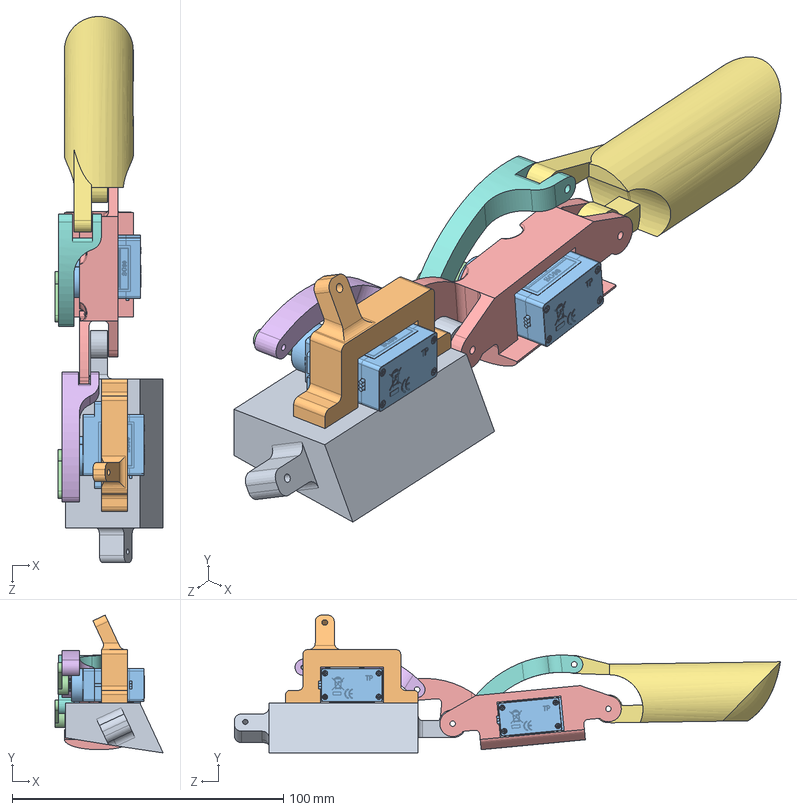
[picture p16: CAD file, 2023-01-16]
S4H2020-SLEARH-master/Mechanics/CAD/Index.SLDASM
39.9 x 50.8 x 201.2 mm
Palm_index
Servo_Holder_index
SG90 - Micro Servo 9g - Tower Pro.1 x 2
SG90 - Micro Servo 9g - Tower Pro.2 x 2
SG90 - Servo Socket
finger_lever_proximal
phalange_Index-MiddleFinger
Finger_lever_distal

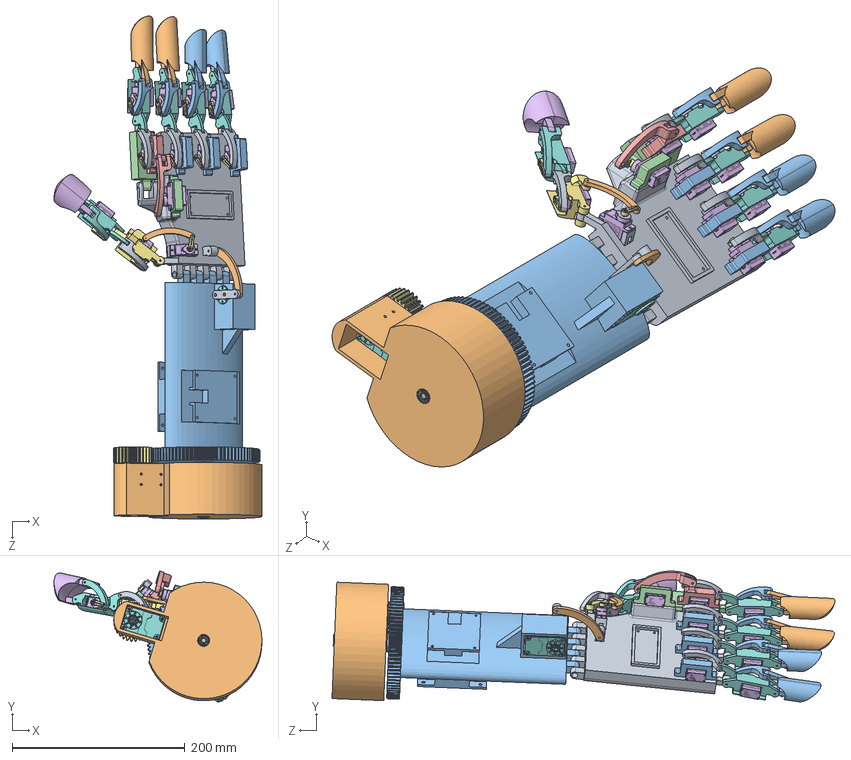
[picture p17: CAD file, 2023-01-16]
S4H2020-SLEARH-master/Mechanics/CAD/hand.SLDASM
240.7 x 151.5 x 582.4 mm
Palm
Base
Arm
8632T144_D-PROFILE SHAFT
plain washer xlarge grade c_iso
Gear
XL-430 x 2
Dynamixel_Coupler
Wrist_lever
ServoHolder x 3
Palm_index
Servo_Holder_index
SG90 - Micro Servo 9g - Tower Pro.1 x 12
SG90 - Micro Servo 9g - Tower Pro.2 x 12
SG90 - Servo Socket x 5
finger_lever_proximal x 4
phalange_Index-MiddleFinger x 2
Finger_lever_distal x 4
ServoHolder -palm_index
palm_index_lever
phalange_thumb
SG90 - Servo Socket_thumb
Thumb_finger_lever_distal
Proximal_thumb_lever
Thumb_lever
phalange_RingFinger-PinkyFinger x 2

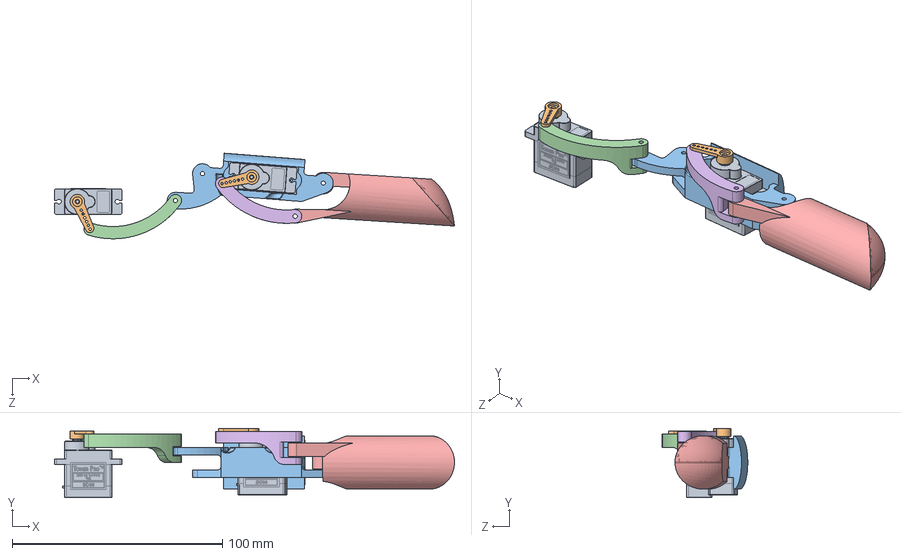
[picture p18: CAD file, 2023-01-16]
S4H2020-SLEARH-master/Mechanics/CAD/Index_MiddleFinger.SLDASM
190.4 x 33.0 x 40.8 mm
SG90 - Micro Servo 9g - Tower Pro.1 x 2
SG90 - Micro Servo 9g - Tower Pro.2 x 2
SG90 - Servo Socket
finger_lever_proximal
phalange_Index-MiddleFinger
Finger_lever_distal

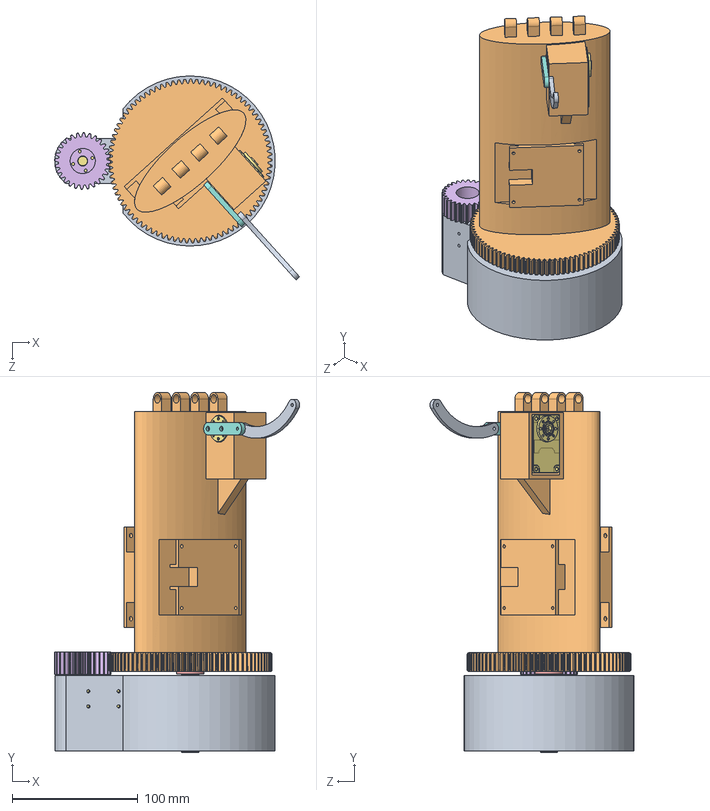
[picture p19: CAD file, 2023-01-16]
S4H2020-SLEARH-master/Mechanics/CAD/Arm_Base_Assembly.SLDASM
194.7 x 285.8 x 162.0 mm
Base
Arm
8632T144_D-PROFILE SHAFT
plain washer xlarge grade c_iso
Gear
XL-430 x 2
Dynamixel_Coupler
Wrist_lever

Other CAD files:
Puissance Gant/Mécanique/doigts/bout majeur doigt.SLDPRT
Puissance Gant/Mécanique/FOREARM1 - Copy.SLDPRT
S4H2022-Sym-Bot-main/Robotic Arm/Material & Assembly/Base/Holding_Ring.SLDPRT
S4H2022-Sym-Bot-main/Robotic Arm/Material & Assembly/Base/STL/coupleur350W.STL
Puissance Gant/Mécanique/Avant-Bras.sldprt
Puissance Gant/Mécanique/Mécanisme_Poignet_1.sldprt
Puissance Gant/Mécanique/Mécanisme_Poignet_2.sldprt
Puissance Gant/Mécanique/Poulie v2 - Copy.SLDPRT
Puissance Gant/Mécanique/Poulie.sldprt
Puissance Gant/Mécanique/doigts/bas annulaire+index doigt.SLDPRT
Puissance Gant/Mécanique/doigts/bas majeur doigt.SLDPRT
Puissance Gant/Mécanique/doigts/bas petit doigt.SLDPRT
Puissance Gant/Mécanique/doigts/bas pouce.SLDPRT
Puissance Gant/Mécanique/doigts/bout annulaire+index doigt.SLDPRT
Puissance Gant/Mécanique/doigts/bout petit doigt.SLDPRT
Puissance Gant/Mécanique/doigts/bout pouce.SLDPRT
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

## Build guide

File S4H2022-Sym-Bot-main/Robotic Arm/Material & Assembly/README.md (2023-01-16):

# Material and Assembly

## Table of Content
- [Material and Assembly](#material-and-assembly)
  - [Table of Content](#table-of-content)
  - [Electrical Components](#electrical-components)
    - [MicroController](#microcontroller)
    - [Dynamixel Motors 1](#dynamixel-motors-1)
    - [Dynamixel Motors 2](#dynamixel-motors-2)
    - [ServoMotors](#servomotors)
    - [Power Supply](#power-supply)
  - [Assembly Info](#assembly-info)
    - [couplerW350](#couplerw350)
    - [Gripper](#gripper)
  - [Electrical Schematic](#electrical-schematic)

## Electrical Components
### MicroController
* Brand : [OpenCr](https://www.robot-advance.com/art-opencr1-0-robotis-2353.htm)
* Model : OpenCr
* Quantity : 1

### Dynamixel Motors 1
* Brand : [Dynamixel](https://emanual.robotis.com/docs/en/software/dynamixel/dynamixel_workbench/)
* Model : XM430-W350
* Quantity : 1

### Dynamixel Motors 2
* Brand : [Dynamixel](https://emanual.robotis.com/docs/en/software/dynamixel/dynamixel_workbench/)
* Model : XM430-W250
* Quantity : 2

### ServoMotors
* Brand : [HiTec](https://www.robotshop.com/ca/en/hitec-hs-422-servo-motor.html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)
* Model : HS-422
* Quantity : 1

### Power Supply
* Brand : [GlobTek inc.](https://www.digikey.ca/en/products/detail/globtek-inc/TR9CE7500LLP-IM-R6B/11201299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)
* Model : GTM96900P9012-T2
* Quantity : 1

## Assembly Info
Assembly schematics and BOMs for each part of the robot (gripper, arm and base) are available in "Material and Assembly" -> "Assembly". Parts that need to be printed can be found in their respective "STL" folder.

### couplerW350
The XM430-W350 Dynamixel motors use a particular coupler in order to support higher torques. The couplerW350 (available under "Miscellaneous") functions as a bridge between the motor and the 545548 hub. To properly assemble the coupler, the following screws should be used:
* 4 x M2x03 socket head
* 4 x 6-32x1/4 socket head

### Gripper
Due to its compactness, the gripper should be assembled in a specific order to tighten every screws properly.
* Assemble the claw tips and the racks through the slots of the casing using the appropriate spacers and washers in between.
* Fix the HS-422 Hitec servomotor to the casing. In order to protect the casing, the use of washers is recommended, but not necessary.
* Install the adaptor. Make sure the cables of the Hitec servomotor bend in a natural way to avoid permanent damage.
* Screw the two parts of the casing together. Make sure the driving gear is in its "open" state by turning it clockwise until it blocks before connecting it with the racks.
* Gently push the claw tips toward each other. If everything went well, the gear should rotate along. The gripper is now ready to use.

## Electrical Schematic
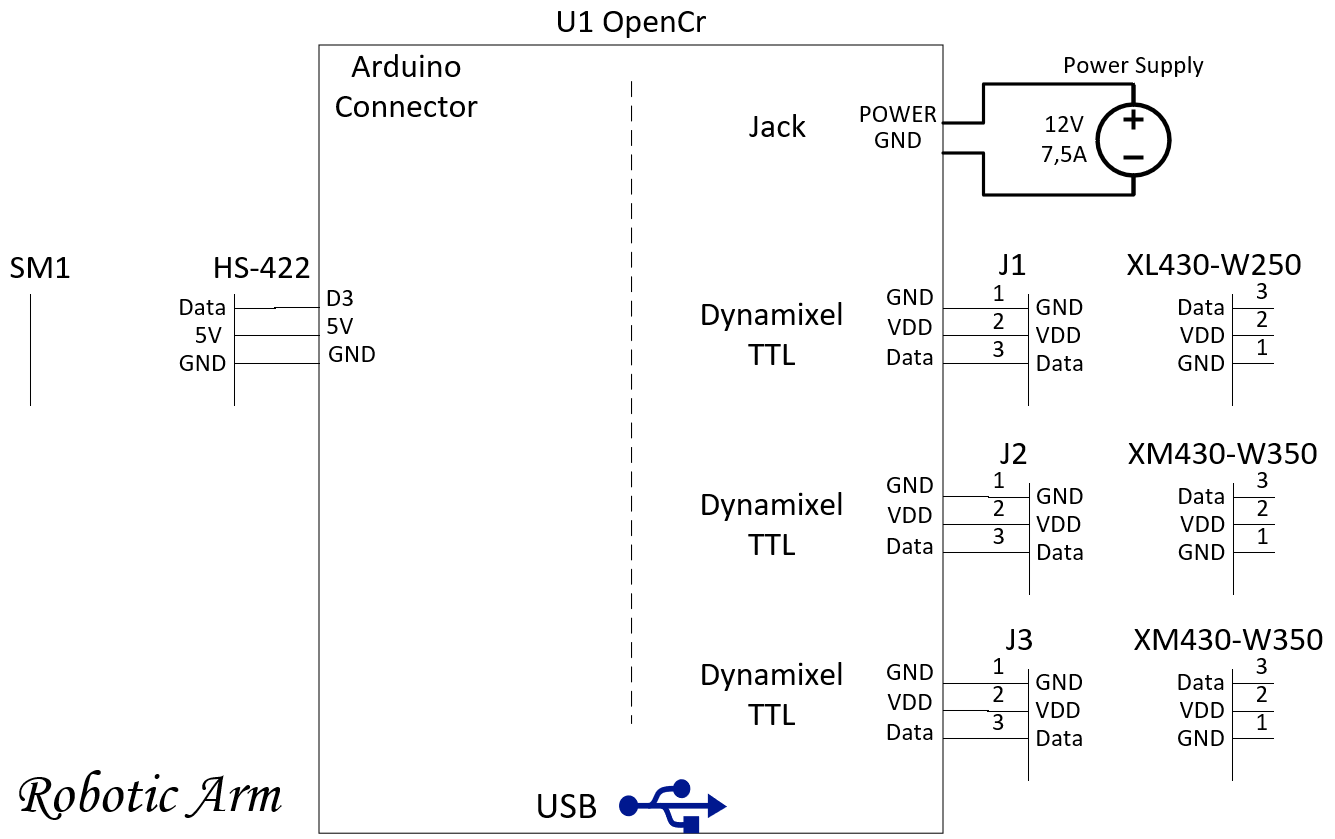
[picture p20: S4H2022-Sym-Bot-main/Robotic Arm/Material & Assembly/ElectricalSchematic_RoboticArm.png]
ElectricalSchematic - RoboticArm


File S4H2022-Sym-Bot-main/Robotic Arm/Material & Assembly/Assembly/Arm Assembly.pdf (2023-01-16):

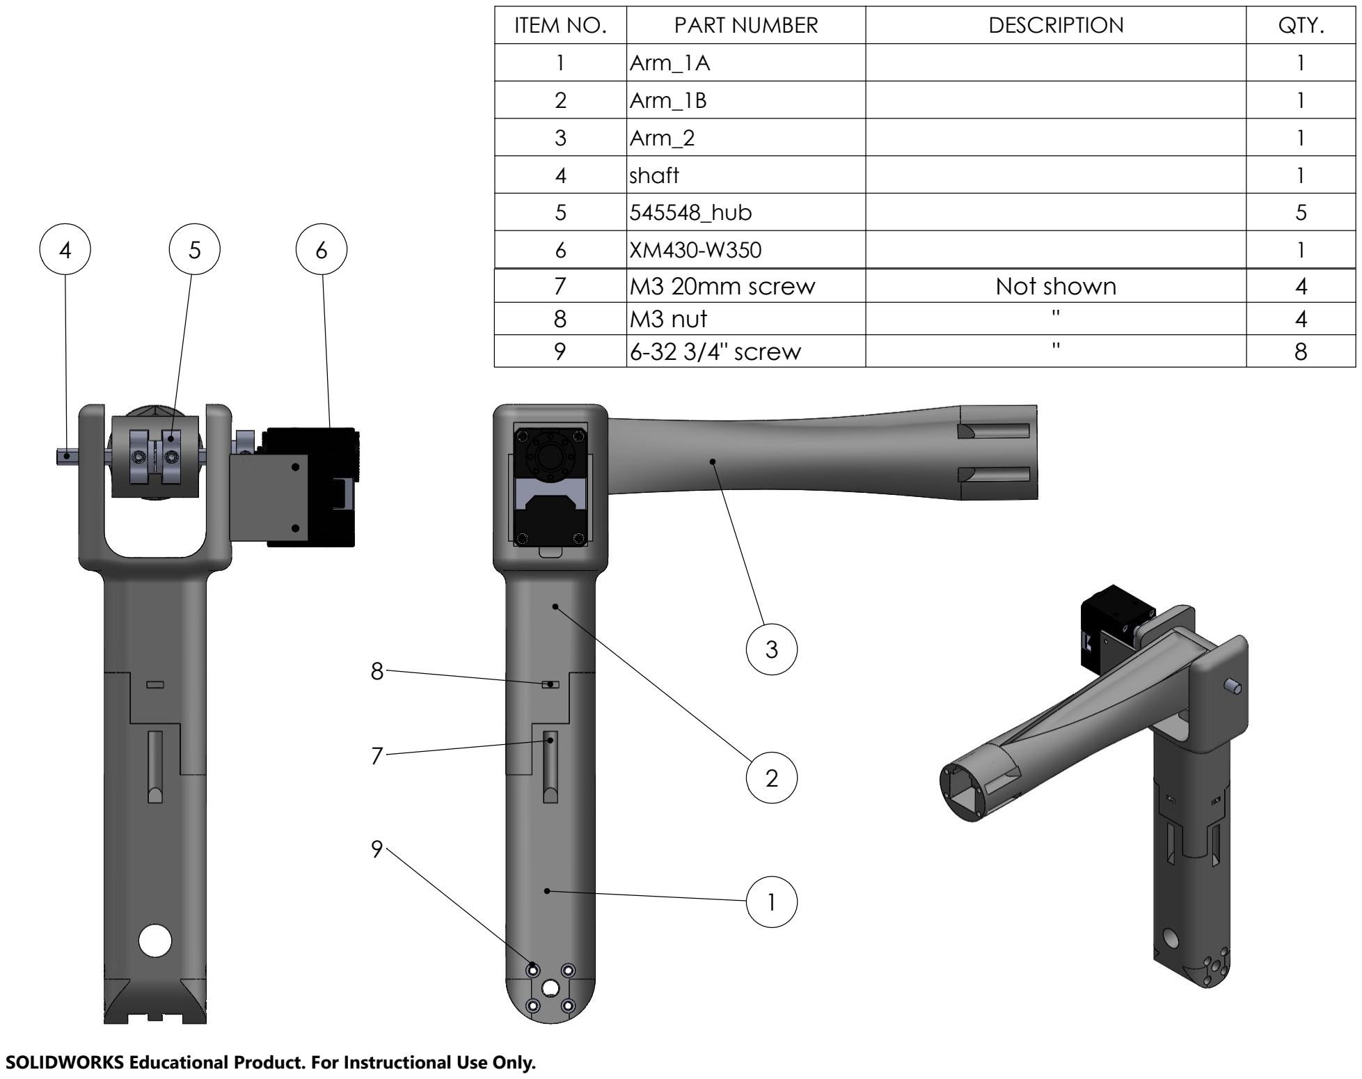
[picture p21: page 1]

ITEM NO. | PART NUMBER | DESCRIPTION | QTY.
1 | Arm_1A | | 1
2 | Arm_1B | | 1
3 | Arm_2 | | 1
4 | shaft | | 1
5 | 545548_hub | | 5
6 | XM430-W350 | | 1
7 | M3 20mm screw | Not shown | 4
8 | M3 nut | " | 4
9 | 6-32 3/4" screw | " | 8

8

7

3

2

1

9

4 | 5 | 6

SOLIDWORKS Educational Product. For Instructional Use Only.

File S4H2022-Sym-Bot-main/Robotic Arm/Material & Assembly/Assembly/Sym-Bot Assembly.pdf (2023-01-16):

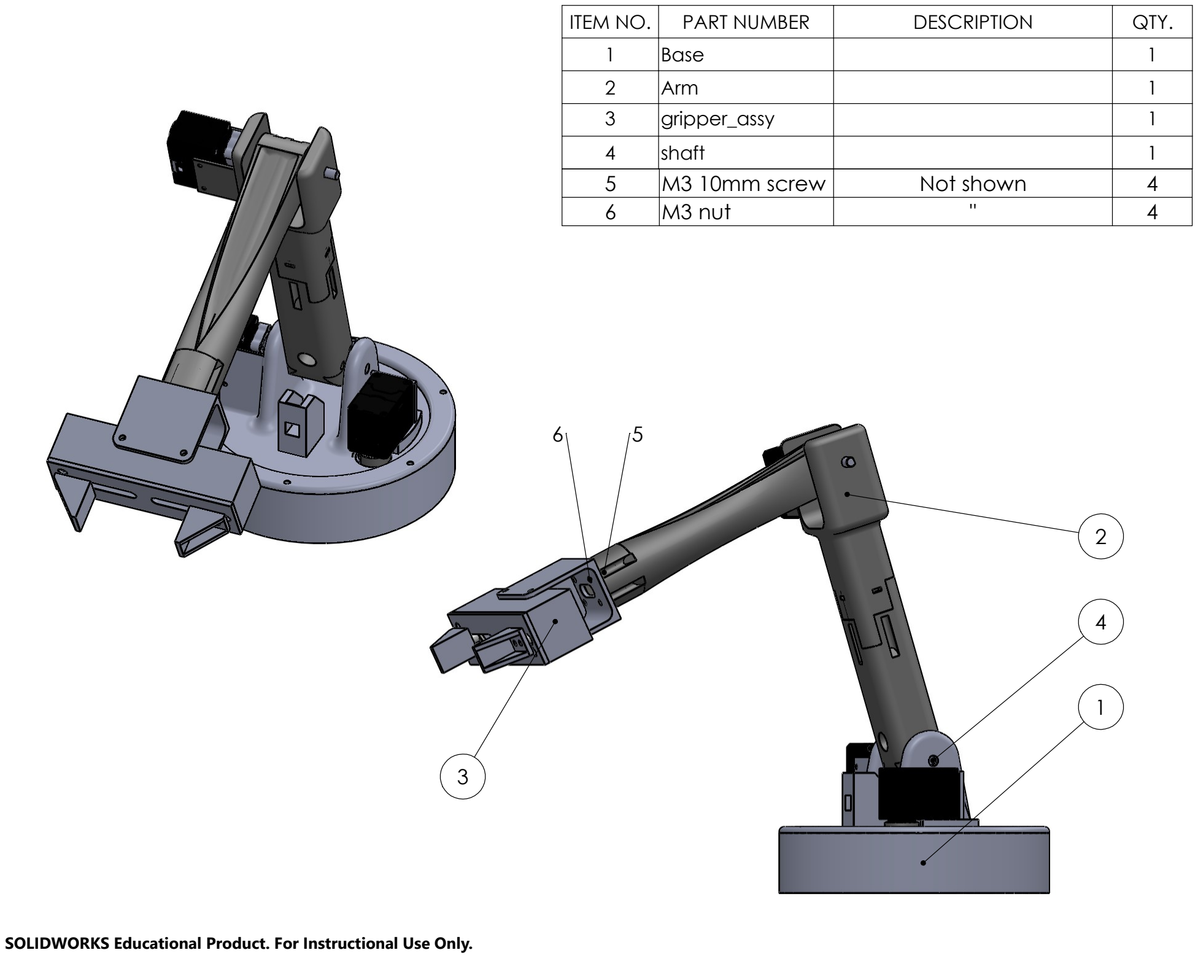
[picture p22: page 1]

1

5

4

3

2

6

ITEM NO. | PART NUMBER | DESCRIPTION | QTY.
1 | Base | | 1
2 | Arm | | 1
3 | gripper_assy | | 1
4 | shaft | | 1
5 | M3 10mm screw | Not shown | 4
6 | M3 nut | " | 4

SOLIDWORKS Educational Product. For Instructional Use Only.

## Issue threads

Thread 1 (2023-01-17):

Choix du type de gant

LudovicComtois, 2023-01-17:
Choisir le type de gant
-Doit être facilement utilisable et modifiable
-Doit être peu cher (acheter en paquet?)

LudovicComtois, 2023-01-25:
Gant de billard ou de construction à 2$ la paire

Closed 2023-01-25.

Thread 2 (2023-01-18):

Trier le code existant

LudovicComtois, 2023-01-18:
Combiner les parties utiles du code existant de la main et du gant afin d'avoir un fichier de code concis.

LudovicComtois, 2023-01-25:
Librairies ajoutées, code non trié, mais nous allons pas mal repartir du départ en s'en inspirant.

Closed 2023-01-25.

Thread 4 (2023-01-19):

Conception de la main - initiale

LudovicComtois, 2023-01-19:
Avoir un prototype de main afin de pouvoir l'imprimer et commencer l'assemblage.

Permettra de faire une preuve de concept du fonctionnement de notre système de servomoteurs et tendons

LudovicComtois, 2023-01-25:
Système de tendons très prometteurs

Closed 2023-01-25.

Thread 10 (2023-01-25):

Nouvelle itération de la main avec doigts fonctionnels

LudovicComtois, 2023-01-25:
Ajouter les modifications discutées et faire imprimer la main. Tester avec les doigts complets (en espérant que Tokyo Drift vole pas les jointures)

Closed 2023-02-15.

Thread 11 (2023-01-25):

Commencer le design du poignet

LudovicComtois, 2023-01-25:
Faire la conception du poignet et de la jointure entre la main et le poignet. Tester l'intégration avec le passage de fil de pêche.

Serait intéressant d'intégrer les moteurs dynamixel dans la conception, mais peut passer au prochain sprint

Closed 2023-02-15.

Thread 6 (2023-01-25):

Faire communiquer l'OpenCR avec un ordinateur / un pi

LudovicComtois, 2023-01-25:
Être capable de lire des données (peu importe le type, peut être le temps écoulé, etc.) envoyées par l'ordinateur/un pi sur un openCR (pour vérifier que les moteurs peuvent fonctionner)

Vérification possible à faire sur l'ordinateur pour confirmer que la donnée a été lue.

LudovicComtois, 2023-02-15:
Communication avec un ordinateur

Closed 2023-02-15.

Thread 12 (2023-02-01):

Créer un prototype de gant

LudovicComtois, 2023-02-01:
Commencer à tester un prototype de gant avec des résistances flexibles

LudovicComtois, 2023-02-15:
Il manque les résistances flexibles pour commencer ça. Fred a commencé à tester avec des potentiomètres pour son code

Closed 2023-04-04.

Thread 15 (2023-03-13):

Optimiser le modèle des doigts

LudovicComtois, 2023-03-13:
Éviter la rotation des doigts lors de l'utilisation

Réduire le temps d'impression et la quantité de matériau utilisé

Rendre un peu plus réaliste si possible

Closed 2023-03-28.

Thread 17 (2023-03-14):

Communiquer entre l'ESP32 et un raspberry pi

LudovicComtois, 2023-03-14:
Utiliser le protocole MQTT pour établir la communication sans fil entre le gant et la station de la main robotisée.

Doit permettre d'envoyer des messages contenant la position à envoyer de chaque moteur ainsi que des informations pour l'interface

LudovicComtois, 2023-03-14:
La communication est fonctionnelle entre les appareils et on peut lire les messages sur le raspberry pi

Closed 2023-03-14.

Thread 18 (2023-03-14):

Communiquer entre le Raspberry Pi et l'OpenCR et faire fonctionner les moteurs

LudovicComtois, 2023-03-14:
Permettre le mouvement des moteurs à partir de commandes envoyées par l'ESP32 et transmises par le Raspberry Pi

LudovicComtois, 2023-03-21:
Communication faite à partir de l'ESP32, on peut recevoir les messages sur l'ordinateur connecté à l'OpenCR. Il reste à lire les messages

Closed 2023-04-04.

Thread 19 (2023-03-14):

Créer une interface (sans programmation)

LudovicComtois, 2023-03-14:
Utiliser Qt Designer et QtPy5 pour créer une interface utilisateur ergonomique et qui contient les informations nécessaires au fonctionnement du robot.

LudovicComtois, 2023-03-14:
Le vide sera est pour un graphique de puissance consommée par les moteurs

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

Closed 2023-03-14.

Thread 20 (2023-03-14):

Programmer l'interface

LudovicComtois, 2023-03-14:
Ajouter les relations entre l'interface et le code de communication :
- Mode manuel pour envoyer des données aux moteurs sans considérer celles du gant
- Recevoir les données de l'OpenCR (position actuelle, énergie, etc)
- Bouton d'urgence pour arrêter les moteurs
- État du gant (communication active, calibration)

LudovicComtois, 2023-03-15:
Section du mode manuel complétée pour l'interaction des boutons et de la console. Il reste à programmer l'envoi des données

LudovicComtois, 2023-04-04:
La communication est complète alors on peut commencer à inclure la lecture de données

LudovicComtois, 2023-04-05:
Ce qui est fait :
- Affichage de la commande de positionnement des moteurs
- Affichage de l'état du serveur et du délai entre chaque commande

Ce qui est en cours :
- Graphique de puissance (mettre la puissance au lieu du délai quand on aura l'OpenCR pour tester
- Envoi des commandes manuelles (ajouter la partie comm et l'affichage de la nouvelle commande)

Ce qui est à faire :
- Passer du mode automatique à manuel dans l'OpenCR
- Bouton d'arrêt d'urgence

LudovicComtois, 2023-04-17:
Interface complète

Closed 2023-04-17.

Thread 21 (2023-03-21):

Créer la documentation du projet

LudovicComtois, 2023-03-21:
Documenter les différentes sections avec un fichier .md

Un utilisateur futur devra être capable de reproduire le projet à l'aide des instructions et des informations fournies

LudovicComtois, 2023-04-17:
Documentation complète avec la remise

Closed 2023-04-17.

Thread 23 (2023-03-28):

Calculs de mécanique

LudovicComtois, 2023-03-28:
Calculer le couple que chaque moteur peut effectuer sur la corde en tension.

Faire une estimation de la force de préhension que les doigts peuvent exercer sur un objet.

LudovicComtois, 2023-04-17:
Estimation faite. 110N de tension dans chaque corde. Les moteurs ne sont pas un enjeu dans la préhension d'objets

Closed 2023-04-17.

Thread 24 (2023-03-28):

Assembler le gant de contrôle

LudovicComtois, 2023-03-28:
1. tester la faisabilité de lanières de velcro pour tenir les résistances (au lieu des embouts bleus)
2. installer la meilleure solution sur le gant
3. Placer le filage du gant selon le schéma actuel des potentiomètres
4. Assembler le protoboard avec le ESP32 et le filage requis
5. placer le protoboard sur la sangle pour avant-bras
6. mettre le IMU dans la boîte de plastique à cet effet
7. relier les résistances par fil jumper vers des rallonges connectées à l'ESP32 (paires de fil de 10 ou 20cm qu'on peut séparer au milieu)
8. Vérifier que le gant fait encore sur une main et qu'il est facilement enfilable

LudovicComtois, 2023-04-17:
Changement des résistances flexibles pour des potentiomètres coulissants.
Bagues de plastique pour tenir du fil de pêche qui tire les potentiomètres. Un élastique retient les potentiomètres pour les ramener à leur position initiale lorsque les doigts sont ouverts.

Plus de détails dans le readme de la section électrique.

Closed 2023-04-17.

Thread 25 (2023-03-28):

Tests de limites de la main, du poignet et de la base

LudovicComtois, 2023-03-28:
Vérifier quelle est la plage de rotation de chaque moteur pour le fonctionnement de la main (savoir quel est le delta de rotation de chaque moteur entre son état initial et l'état de main fermée)
Vérifier aussi quel est la consommation de la main lorsqu'on ramasse un objets (et que les moteurs forcent pour le tenir)

Closed 2023-04-05.

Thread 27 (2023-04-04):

Créer une routine de calibration du gant

LudovicComtois, 2023-04-04:
Faire en sorte qu'en appuyant sur le bouton du gant, on puisse faire la calibration des positions maximales et minimales de la main.

Cette routine doit être reliée à l'interface

LudovicComtois, 2023-04-17:
Calibration abandonnée puisqu'on a changé les résistances flexibles pour des potentiomètres coulissants

Closed 2023-04-17.

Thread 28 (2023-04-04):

Intégrer les mouvements des moteurs à l'assemblage de la main

LudovicComtois, 2023-04-04:
Tester les limites des moteurs et les implémenter dans le code de l'OpenCR afin de bien représenter les mouvements de la main. (avoir une plage de mouvements entre l'ouverture et la fermeture des doigts représentant les positions que le moteur doit prendre)

Closed 2023-04-17.

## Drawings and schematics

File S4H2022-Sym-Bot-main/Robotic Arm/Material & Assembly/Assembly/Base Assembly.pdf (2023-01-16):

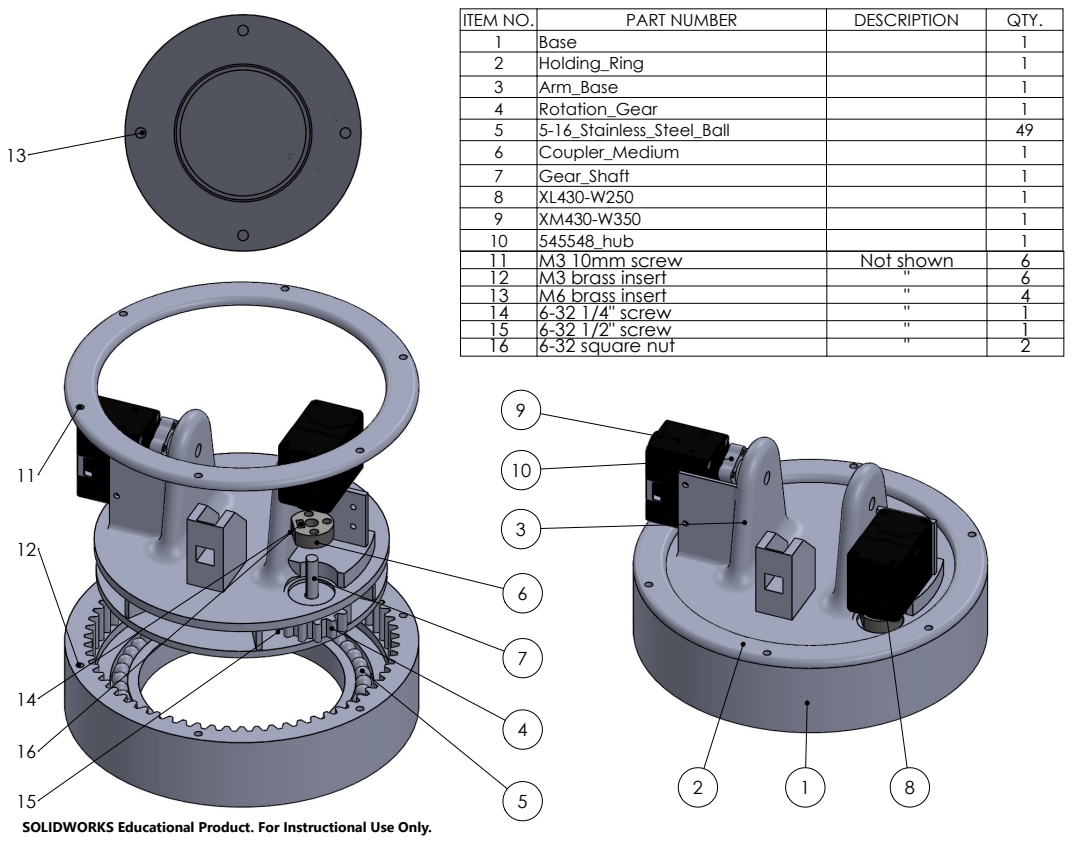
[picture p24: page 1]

ITEM NO. | PART NUMBER | DESCRIPTION | QTY.
1 | Base | | 1
2 | Holding_Ring | | 1
3 | Arm_Base | | 1
4 | Rotation_Gear | | 1
5 | 5-16_Stainless_Steel_Ball | | 49
6 | Coupler_Medium | | 1
7 | Gear_Shaft | | 1
8 | XL430-W250 | | 1
9 | XM430-W350 | | 1
10 | 545548_hub | | 1
11 | M3 10mm screw | Not shown | 6
12 | M3 brass insert | " | 6
13 | M6 brass insert | " | 4
14 | 6-32 1/4" screw | " | 1
15 | 6-32 1/2" screw | " | 1
16 | 6-32 square nut | " | 2

SOLIDWORKS Educational Product. For Instructional Use Only.

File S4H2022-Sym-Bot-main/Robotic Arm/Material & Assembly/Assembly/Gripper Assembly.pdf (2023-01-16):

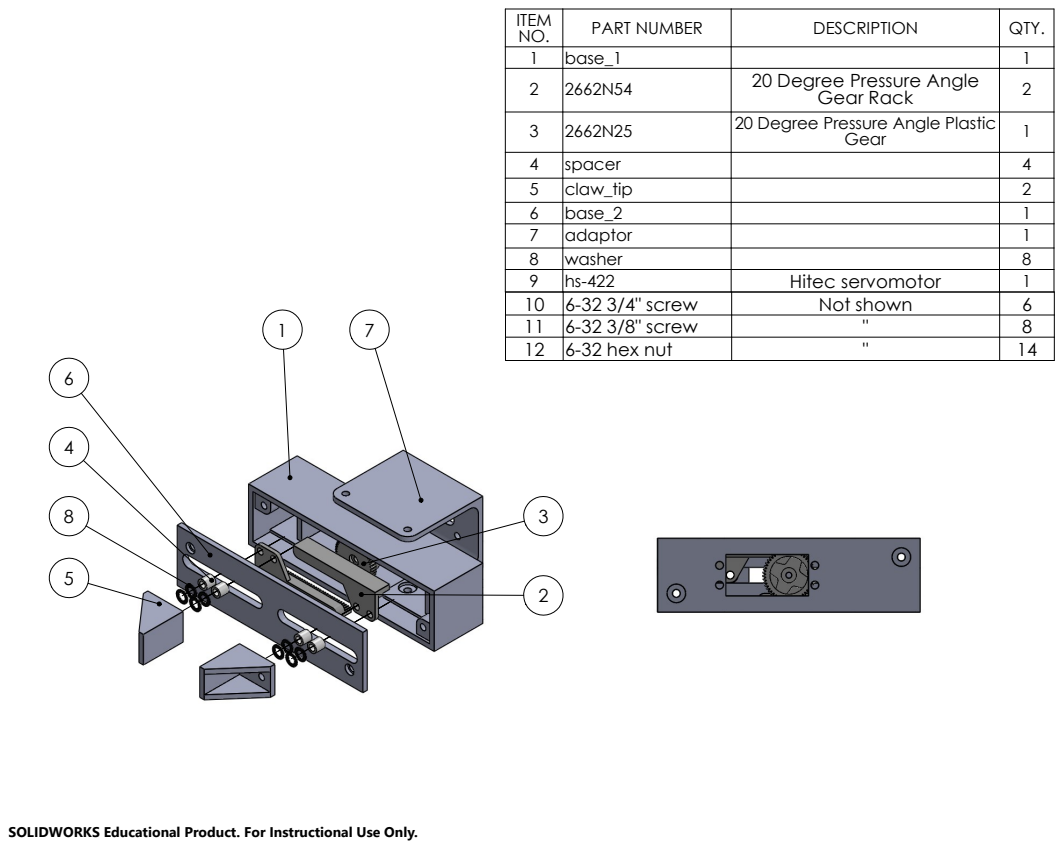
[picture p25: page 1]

ITEM NO. | PART NUMBER | DESCRIPTION | QTY.
1 | base_1 | | 1
2 | 2662N54 | 20 Degree Pressure Angle Gear Rack | 2

3 | 2662N25 | 20 Degree Pressure Angle Plastic Gear | 1

4 | spacer | | 4
5 | claw_tip | | 2
6 | base_2 | | 1
7 | adaptor | | 1
8 | washer | | 8
9 | hs-422 | Hitec servomotor | 1
10 | 6-32 3/4" screw | Not shown | 6
11 | 6-32 3/8" screw | " | 8
12 | 6-32 hex nut | " | 14

SOLIDWORKS Educational Product. For Instructional Use Only.

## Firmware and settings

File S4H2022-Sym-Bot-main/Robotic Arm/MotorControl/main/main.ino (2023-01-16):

/**
 *  Implement all the motor control part on OpenCr Board
 *    and communication management over Serial/Json
 * 
 *  Autors  : Handling-GRO, 65th promotion students, UdeS Genie de Robotique
 *  Date    : 2021-04-16
 * 
 *  Modification
 *    Initialise all the motors in setup
 *    Motor's Inheritance (Servomotor & Dynamixel)
 *    Use only CMD : GO_TO_JOINT_INDEX, GO_TO_HOME_INDEX & GO_TO_JOG
 *  Autors  : Sym-Bot, 66th promotion students, UdeS Genie de Robotique
 *  Date    : 2021-04-14
 * 
 */

// ============================================================================
// ================================= INCLUDE ==================================
// ============================================================================
#include <Arduino.h>

#include "MessageIO.h"
#include "SerialComm.h"

#include "DynamixMotor.h"
#include "ServoMotor.h"

// ============================================================================
// =============================== DEFINE/CONST ===============================
// ============================================================================
#define DEBUG 0                           // 0: Disable | 1 : Enable debug code
                                          // Comment to disable print
#define DEBUG_MSG(msg)                    // Serial.print(msg)
#define DEBUG_MSG_LN(msg)                 // Serial.println(msg)

#define BAUD              57600           // Serial's Baud

#define NbrMotorDynamixel 3
#define NbrMotorServo     1
const uint8_t NBR_MOTOR   = NbrMotorDynamixel + NbrMotorServo;

// ============================================================================
// ================================ ENUM/STRUCT ===============================
// ============================================================================
// Command index received from PI
enum CMD
{
  // ACTION IN [21, 29]
  GO_TO_JOINT_INDEX                =  1,       // USED BY SYM-BOT PROJECT
  GO_TO_HOME_INDEX                =  2,       // USED BY SYM-BOT PROJECT
  GO_TO_JOG_INDEX                 =  3,       // USED BY SYM-BOT PROJECT
  ACTION_OPEN_GRIPPER             =  5,
  ACTION_CLOSE_GRIPPER            =  6,
  ACTION_POSITION_GRIPPER         =  7,
  // SET VALUE IN [01, 09]
  SET_ZERO_POSITION_INDEX         = 11,
  SET_HOME_POSITION_INDEX         = 12,
  SET_MAX_POSITION_INDEX          = 13,
  // RETURN VALUE IN [11, 19]
  RETURN_ZERO_POSITION_INDEX      = 21,
  RETURN_HOME_POSITION_INDEX      = 22,
  RETURN_MAX_POSITION_INDEX       = 23,
  RETURN_ACTUAL_POSITION_INDEX    = 27
};

// ============================================================================
// ============================= VARIABLE GLOBALE =============================
// ============================================================================
MessageIO IO;
SerialComm SC(&Serial);
Motor *motors[NBR_MOTOR];

// ============================================================================
// ============================ DECLARED FUCNTION =============================
// ============================================================================
void init_dynamix();
void init_servo();

// ============================================================================
// =============================== SETUP/LOOP =================================
// ============================================================================
void setup() {
  // Initialise Serial Comm
  Serial.begin(BAUD);
  IO.addDevice(&SC);

  delay(10);

  // Initialise all motors and goto home each
  init_dynamix();
  init_servo();
}

void loop() {
  // MESSAGE HANDLING BLOCK, COMMUNICATION
  ControlMessage* msg = IO.readMessage(0);

  if (msg == nullptr) {
    // THIS CODE FOR TROUBLESHOOTING
    #if DEBUG == 1
      auto responce = ControlMessage(-1);
      IO.sendMessage(0,responce);
    #endif
  }
  else {
    // PAYLOAD MANAGEMENT FOR EACH ENGINE
    for (size_t i = 0; i < NBR_MOTOR; ++i) {
      // CODE FOR THE DIFFERENT OPERATIONS TO BE CARRIED OUT BY THE ENGINES
      switch (msg->getType()) {
        // VALUE THAT DOESN'T MATCH ANY OF THE CASE
        default:
          break;
        // CODE TO ACTION' MOTOR
        case GO_TO_JOINT_INDEX:
          motors[i]->go_to_degrees(msg->getPayload()[i]);
          break;
        case GO_TO_HOME_INDEX:
          motors[i]->go_to_home();
          break;
        case GO_TO_JOG_INDEX:
          if (msg->getPayload()[i] == 1)
            motors[i]->go_forward();
          else if (msg->getPayload()[i] == -1)
            motors[i]->go_backward();
          else { 
            // The arm doesn't move
          }
          break;
        case ACTION_OPEN_GRIPPER:
          if (i >= NbrMotorDynamixel)
            motors[i]->go_backward();
          break;
        case ACTION_CLOSE_GRIPPER:
          if (i >= NbrMotorDynamixel)
            motors[i]->go_forward();
          break;
        case ACTION_POSITION_GRIPPER:
          if (i >= NbrMotorDynamixel)
            motors[i]->go_to_degrees(msg->getPayload()[i]);
          break;
        
        //CODE TO SET INFORMATION
        case SET_ZERO_POSITION_INDEX:
          motors[i]->set_zero(msg->getPayload()[i]);
          break;
        case SET_HOME_POSITION_INDEX:
          motors[i]->set_home(msg->getPayload()[i]);
          break;
        case SET_MAX_POSITION_INDEX:
          motors[i]->set_max_limit(msg->getPayload()[i]);
          break;

        //CODE TO RETURN INFORMATION
        case RETURN_ZERO_POSITION_INDEX:
          msg->getPayload()[i] = (motors[i]->get_zero());
          break;
        case RETURN_HOME_POSITION_INDEX:
          msg->getPayload()[i] = motors[i]->get_home();
          break;
        case RETURN_MAX_POSITION_INDEX:
          msg->getPayload()[i] = motors[i]->get_max_limit();
          break;
        case RETURN_ACTUAL_POSITION_INDEX:
          msg->getPayload()[i] = (motors[i])->get_position();
          break;
      }
    }
    
    if(msg->getType() > 20) {
        ControlMessage response(msg->getType(), msg->getPayLoadSize(), msg->getPayload());
        IO.sendMessage(0, response);
    }

    // RELEASE msg FROM THE HEAP
    delete msg;
  }

  // delay(5);
}

// ============================================================================
// ============================ IMPLEMENT FUCNTION ============================
// ============================================================================
/* Function initialise the dynamixel motors and goto home */
void init_dynamix() {
  const uint8_t  IDs[]        = {    1,     2,     3};
  const uint16_t ZEROs[]      = {   10,  1360,  1136};
  const uint16_t HOMEs[]      = { 2047,  1920,  2160};
  const uint16_t MAXs[]       = { 4090,  2384,  3184};
  const uint16_t VELOCITYs[]  = {  128,    32,    32};
  const bool REVERSEs[]       = {false, false,  true};

  // INITIALIZE DYNAMIXEL MOTORS
  for (size_t m = 0; m < NbrMotorDynamixel; ++m) {
    if (motors[m] == nullptr) {
      motors[m] = new DynamixMotor(IDs[m], ZEROs[m], HOMEs[m], MAXs[m], VELOCITYs[m], REVERSEs[m]);
      DEBUG_MSG_LN("SET DYNAMIXEL");
    }
  }

  // GOTO HOME
  for (size_t m = 0; m < NbrMotorDynamixel; ++m) {
    motors[m]->go_to_home();

    DEBUG_MSG("Homing  ");
    DEBUG_MSG_LN(m);
  }
}

/* Function initialise the servo motors and goto home */
void init_servo() {
  const uint8_t IDs[]         = {3};

  // INITIALIZE SERVO MOTORS
  for (size_t m = NbrMotorDynamixel; m < NBR_MOTOR; ++m) {
    if (motors[m] == nullptr) {
      motors[m] = new ServoMotor(IDs[m-NbrMotorDynamixel]);
      DEBUG_MSG_LN("SET SERVO");
    }
  }

  // GOTO HOME
  for (size_t m = NbrMotorDynamixel; m < NBR_MOTOR; ++m) {
    motors[m]->go_to_home();

    DEBUG_MSG("Homing ");
    DEBUG_MSG_LN(m);
  }
}

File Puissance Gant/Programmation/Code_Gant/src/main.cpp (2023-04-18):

#include <Arduino.h>
#include "WiFi.h"
#include "PubSubClient.h" // Connect and publish to the MQTT broker

// Pins
#define POUCE 36
#define INDEX 39
#define MAJEUR 34
#define BOUTON 35


// Communication:
String serialData; // String qui est envoyé en Serial au pi4 pour êytre lut et transmit au OpenCR
/// Structure qui contient toute les information de la main
struct Hand
{
    static const uint8_t DOIGTS = 3;            // Nombre de doigt sur le gant 

    int pin[DOIGTS] = {POUCE, INDEX, MAJEUR};
    uint16_t fingers[DOIGTS] = {0, 0, 0};       // Order for the right hand: {POUCE INDEX MAJEUR}
    float max[DOIGTS] = {4096, 4096, 4096};     // Valeur maximum des resistances
    float min[DOIGTS] = {0, 0, 0};              // Valeur minimum des resistances

    int etape = 0;                              // État de la calibration 
} hand = {};


// Wifi
// Il est important de noter que le wifi est utilisé en connection en point d'accès avec un ordinateur portable ou un cellulaire
const char* ssid = "ludo";                          // Nom du réseau personnelle
const char* wifi_password = "puissance";            // Mot de passe du réseau

// MQTT
// mosquitto est le mqtt broker utiliser du au fait qu'il est gratuit et open-source
const char* mqtt_server = "192.168.137.254";  // IP of the MQTT broker
const char* resistance_topic = "Eq7_PuissanceGant_S4/gant/commandes";
const char* calibration_topic = "Eq7_PuissanceGant_S4/gant/calibration";
const char* mqtt_username = "puissance"; // MQTT username
const char* mqtt_password = "puissance"; // MQTT password
const char* clientID = "gant"; // MQTT client ID

// Initialise the WiFi and MQTT Client objects
WiFiClient wifiClient;
// 1883 is the listener port for the Broker
PubSubClient client(mqtt_server, 1883, wifiClient); 

/*-------------------------------------------------- setup functions --------------------------------------------------*/
// Mode des pin pour la lecture des données
void setupFlexSensors()
{
    pinMode(POUCE, INPUT);
    pinMode(INDEX, INPUT);
    pinMode(MAJEUR, INPUT);
    // pinMode(BOUTON, INPUT);
}

// Connexion au Wifi
void connect_WIFI(){
    Serial.print("Connection à ");
    Serial.println(ssid);

    // Connect to the WiFi
    WiFi.begin(ssid, wifi_password);

    // Wait until the connection has been confirmed before continuing
    while (WiFi.status() != WL_CONNECTED) {
        delay(500);
        Serial.print(".");
    }

    Serial.println(".");
    Serial.println("Connecter au Wifi");
}

// Connexion au au serveur MQTT
void connect_MQTT(){
    Serial.println("Connecter au Wifi");
    Serial.print("Adresse IP: ");
    Serial.println(WiFi.localIP());

    if (client.connect(clientID, mqtt_username, mqtt_password)) {
     Serial.println("Connecter au serveur MQTT!");
    }
    else {
        Serial.println("Connection to MQTT Broker failed...");
    }
}


/*-------------------------------------------------- loop functions --------------------------------------------------*/
// Prend la valeur des résistances
void flexSensorsData()
{
    for (int finger = 0; finger < hand.DOIGTS; finger++)
    {
        int val = analogRead(hand.pin[finger]);
        if  (val >= hand.max[finger])
        {
            hand.fingers[finger] = 100; 
        }
        else if (val <= hand.min[finger])
        {
            hand.fingers[finger] = 0; 
        }

        else if ( hand.min[finger] <  val < hand.max[finger])
        {
            hand.fingers[finger] = round((val - hand.min[finger]) / (hand.max[finger] - hand.min[finger]) * 100) ;
        }
    }
}

// Cette fonction correspond au processus de calibration du gant. Elle est activé lorsque le bouton est appuyé. 
/*
void calibration()
{
    delay(500);

    Serial.println("Etape 1");

    if (client.publish(calibration_topic, String(hand.etape).c_str())) {
        // Serial.println(String(hand.etape));
    }

    else {
        //Serial.println("Resistance failed to send. Reconnecting to MQTT Broker and trying again");
        client.connect(clientID, mqtt_username, mqtt_password);
        delay(10); // This delay ensures that client.publish doesn't clash with the client.connect call
        client.publish(calibration_topic, String(hand.etape).c_str());
    }

    while(hand.etape == 1)
    {
        if (digitalRead(BOUTON) == 1)
        {
            for (int finger = 0; finger < hand.DOIGTS; finger++)
            {
                hand.min[finger] = analogRead(hand.pin[finger]);
            }
            hand.etape = 2; 
        } 
    }

    if (client.publish(calibration_topic, String(hand.etape).c_str())) {
        // Serial.println(String(hand.etape));
    }

    else {
        //Serial.println("Resistance failed to send. Reconnecting to MQTT Broker and trying again");
        client.connect(clientID, mqtt_username, mqtt_password);
        delay(10); // This delay ensures that client.publish doesn't clash with the client.connect call
        client.publish(calibration_topic, String(hand.etape).c_str());
    }

    delay(500);
    hand.etape = 2;
    Serial.println("Etape 2");

    while(hand.etape == 2)
    {
        if (digitalRead(BOUTON) == 1)
        {
            for (int finger = 1; finger < hand.DOIGTS; finger++)
            {
                hand.max[finger] = analogRead(hand.pin[finger]);
            }
            hand.etape = 3; 
        } 
    }
    
    if (client.publish(calibration_topic, String(hand.etape).c_str())) {
        // Serial.println(String(hand.etape));
    }

    else {
        //Serial.println("Resistance failed to send. Reconnecting to MQTT Broker and trying again");
        client.connect(clientID, mqtt_username, mqtt_password);
        delay(10); // This delay ensures that client.publish doesn't clash with the client.connect call
        client.publish(calibration_topic, String(hand.etape).c_str());
    }

    delay(500);
    hand.etape = 3;
    Serial.println("Etape 3");

    while(hand.etape == 3)
    {
        if (digitalRead(BOUTON) == 1)
        {
            hand.max[0] = analogRead(hand.pin[0]);
            hand.etape = 0; 
        } 
    }

    delay(500);

    if (client.publish(calibration_topic, String(hand.etape).c_str())) {
        // Serial.println(String(hand.etape));
    }

    else {
        Serial.println("Resistance failed to send. Reconnecting to MQTT Broker and trying again");
        client.connect(clientID, mqtt_username, mqtt_password);
        delay(10); // This delay ensures that client.publish doesn't clash with the client.connect call
        client.publish(calibration_topic, String(hand.etape).c_str());
    }
}
*/
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

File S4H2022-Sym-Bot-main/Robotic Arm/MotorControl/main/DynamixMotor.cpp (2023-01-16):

#include "DynamixMotor.h"

DynamixelWorkbench dxl_wb;  // create DynamixelWorkbench object to control dynamixelS

/**
 * This function initialises a DynamixMotor object
 * 
 * @param id contains the ID of dynamixel motor
 * @param zero the position of motor corresponding to its zero (STEP)
 * @param home the position of motor corresponding to home (STEP)
 * @param max_limmit the position of motor corresponding to its max value (STEP)
 * @param speed the speed of motor corresponding to its velocity
 * @param reverse indicates if motor has to turn the other side
*/
DynamixMotor::DynamixMotor(uint8_t id, uint16_t zero, uint16_t home, uint16_t max_limit, uint16_t speed, bool reverse) {
    this->id = id;

    this->zero      = zero;
    this->home      = home;
    this->max_limit = max_limit;
    this->velocity  = speed;
    this->step      = speed >> 2;
    this->reversed  = reverse;

    cmdSucceeded = dxl_wb.init(DEVICE_NAME, baud);
    cmdSucceeded = dxl_wb.ping((int8_t)id, &model_number, &log);

    if (reverse)
        cmdSucceeded = dxl_wb.setReverseDirection(id, &log);
    else
        cmdSucceeded = dxl_wb.setNormalDirection(id, &log);

    cmdSucceeded = dxl_wb.jointMode(id, this->velocity, 0, &log);    
    cmdSucceeded = dxl_wb.ledOn((uint8_t)id, &log);

    /* Unit	0.229 [rev/min]	Sets velocity of the Profile
       * Unit	1 [msec]	Sets the time span for the Profile
       * Range	0 ~ 32767	‘0’ represents an infinite velocit */
    cmdSucceeded = dxl_wb.itemWrite(id, "Profile_Velocity", this->velocity, &log);
    /* Unit	214.577 [rev/min2]	Sets acceleration of the Profile
       * Unit	1 [msec]	Sets accelerating time of the Profile
       * Range	0 ~ 32767	‘0’ represents an infinite acceleration */
    cmdSucceeded = dxl_wb.itemWrite(id, "Profile_Acceleration", this->accelaration, &log);

    // TO ADD FOR MORE SECURITY
    // cmdSucceeded = dxl_wb.itemWrite(id, "Max_Position_Limit", max_limit, &log);
    // cmdSucceeded = dxl_wb.itemWrite(id, "Min_Position_Limit", zero, &log);
}

void DynamixMotor::go_to(int16_t pos) {
    if (pos < zero)
        pos = zero;
    if (pos > max_limit)
        pos = max_limit;
    position = pos;
    dxl_wb.goalPosition(id, (int32_t)pos, &log);
};

// CONVERT STEP TO DEGREES := 4096 STEP / 360 DEGREES = 11,3778 STEP BY DEGREES
void DynamixMotor::go_to_degrees(int16_t pos) { this->go_to((pos * 11.3778) + zero); }
void DynamixMotor::go_to_home() { this->go_to(home); }

void DynamixMotor::go_forward() {
    int32_t pos = position;
    // int32_t pos = get_position();        // DON'T WORK WITH GRIPPER
    pos -= step;
    go_to(pos);
};

void DynamixMotor::go_backward() {
    int32_t pos = position;
    // int32_t pos = get_position();        // DON'T WORK WITH GRIPPER
    pos += step;
    go_to(pos);
}

int16_t DynamixMotor::get_position() {
    int32_t data = 0;
    cmdSucceeded = dxl_wb.itemRead(id, "Present_Position", &data, &log);
    return data;
}

// DONT USE IN SYM-BOT PROJECT
int16_t DynamixMotor::get_home_offset() {
    int32_t data = 0;
    cmdSucceeded = dxl_wb.itemRead(id, "Homing_Offset", &data, &log);
    return data;
}

void DynamixMotor::setHomingOffset(int16_t pos) {
    cmdSucceeded = dxl_wb.itemWrite(id, "Homing_Offset", pos, &log);
}

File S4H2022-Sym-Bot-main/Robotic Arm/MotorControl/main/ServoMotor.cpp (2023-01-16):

#include "ServoMotor.h"

/**
 * This function initialises a ServoMotor object
 * 
 * @param pin // attaches the servo on this pin to the servo object
 * @param home the position of motor corresponding to home (DEGREES)
*/
ServoMotor::ServoMotor(uint8_t pin, uint16_t home) {
    this->pin = pin;
    this->home = home;
    servo.attach(pin);
    #if DEBUG == 1
        if (servo.attached())
            Serial.print("Ready motor : ");
        else
            Serial.print("Not ready motor : ");
        Serial.println(pin);
    #endif
};

// servo.write(angle), angle: the value to write to the servo, from 0 to 180
void ServoMotor::go_to(int16_t pos) { servo.write(pos); };
void ServoMotor::go_to_degrees(int16_t pos) { this->go_to(pos); }
void ServoMotor::go_to_home() { this->go_to(this->home); }
void ServoMotor::go_forward() { this->go_to(30); };
void ServoMotor::go_backward() { this->go_to(180); }

// Return : The angle of the servo, from 0 to 180 degrees.
int16_t ServoMotor::get_position() { return servo.read(); }
// DONT USE IN SYM-BOT PROJECT
int16_t ServoMotor::get_home_offset() { return 0; }
void ServoMotor::setHomingOffset(int16_t pos) { ; }

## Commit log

2023-01-16 Ajout anciens projets
    Ajout des répertoires GIT des projets sur lesquels on va se baser
    [5-16_Stainless_Steel_Ball.SLDPRT, 535198.SLDPRT, 545548_hub.SLDASM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]
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2023-01-17 Revert "Enlever les licenses"
    This reverts commit 41ee69b3f178fbab34020a55197ff3e9295d4849.
2023-01-17 Update BOM_slirus
    Modifié le nom de leur BOM. Notre BOM est sur teams
    [BOM_SLIRUS.xlsx]
2023-01-19 Ajout des fichiers de code des anciens projets
2023-01-19 Librairies ajoutées
    certaines libs sont en commentaires, car conflit ou impertinentes.
    Librairies provenant de GitHub
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2023-02-11 Faire fonctionner comm avec OpenCR
    Ajuster le code d'arduino pour éviter le problème de reset de l'openCR
2023-02-12 Communication Pi - OpenCR : moteurs
    Modifier la valeur de position de la struct moteurs à partir du code Python.
2023-02-18 Communication et contrôle des moteurs
2023-02-21 Ménage dans les dossiers
    [5-16_Stainless_Steel_Ball.SLDPRT, 535198.SLDPRT, 545548_hub.SLDASM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]
2023-02-22 deleted: GantUI/.gitignore deleted: GantUI/.vscode/extensions.json deleted: GantUI/include/README deleted: GantUI/lib/README deleted: GantUI/platformio.ini deleted: GantUI/src/main.cpp deleted: GantU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
2023-02-22 Revert " deleted: GantUI/platformio.ini"
    This reverts commit b69dfe0adc56d9894f4f11d3f57b9048a5409299.
    [main.cpp]
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2023-02-22 new file: Puissance Gant/Programmation/Code_Gant/.gitignore deleted: Puissance Gant/Programmation/Code_Gant/.pio/build/esp32doit-devkit-v1/.sconsign39.dblite deleted: Puissance Gant/Programmation/Cod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
2023-03-12 Création de l'interface (sans code)
    Comprend les fichiers de test (à supprimer dans le futur, mais servent de référence)
2023-03-15 Début de la ligne de communication (console)
    Lire et écrire le texte entré par l'utilisateur dans la console
2023-03-15 Suite du mode manuel
    La console reçoit la commande du mode manuel et vérifie qu'elle est dans le bon format
2023-03-15 Organisation des dossiers de code
    Changer le dossier Code_Pi pour le séparer en Code_Communication et Code_Interface
2023-03-21 Organisation du dossier Mécanique
    [Assemblage-total.sldasm, FOREARM1.sldprt, Mécanisme poignet 1.sldprt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]
2023-03-22 petites modif du code openCR
    Pas de changement de logique majeur, surtout pour enlever des erreurs de librairie dynamixel
2023-03-29 Optimisation de la comm sérielle de l'OpenCR
    Pousser les limites de la comm OpenCR selon le nombre de moteurs à faire bouger et les messages renvoyés.
    Pour le moment, envoyer 3 moteurs à chaque 100ms et envoyer quelques messages (dont la puissance à chaque 500ms) de l'OpenCR semble fonctionner.
    C'est plutôt serré dans les limites de la comm. L'OpenCR ne lit pas très rapidement son buffer...
2023-03-29 Préparation du test des limites des moteurs
2023-03-30 Ajouter le filtrage des envois de commande de moteurs
    Fait en sorte qu'on diminue la taille des messages envoyés si un ou des moteurs n'ont pas beaucoup bougé, car on n'envoie pas leur valeurs à l'OpenCR.
2023-03-31 va et vien de comm OpenCR
    Pas grand chose a changé, rip mon après-midi
2023-04-05 dernière itération du gant
    dernière itération du gant
    [Mécanisme poignet 2.SLDPRT, bas annulaire+index doigt.SLDPRT, bas majeur doigt.SLDPRT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]
2023-04-05 Interface suite
    Graphique de l'interface (pour le moment avec la latence, mettre la puissance quand l'OpenCR sera connecté
2023-04-12 Continuer Interface
    Envoyer les commandes de mouvement manuel au serveur MQTT
    Continuer les interactions entre l'interface et les messages reçus/envoyés
    Interaction du bouton d'arrêt d'urgence et les commandes améliorées
2023-04-12 Continuer l'interface
    Ajustements de l'apparence
    Commencer avec le mode manuel au lieu d'automatique
    Ajouter l'affichage des commandes manuelles dans les dernières commandes envoyées
2023-04-12 Tester le positionnement des doigts
    Ajouter les plages de mouvement de chaque doigt (manque de lousser/délousser les doigts quand le poignet bouge)
2023-04-13 Déboguer openCR et interface
    Plage de mouvement des doigts est OK, il resterait quelques ajustements si le temps le permet
    L'arrêt d'urgence arrête les moteurs (torque = off)
2023-04-13 Mouvements automatiques et manuels complets
    Il manque seulement d'intégrer la calibration du gant dans l'interface
2023-04-13 Add files via upload
    Assemblage total de la dernière itération de l'avant bras
    [Assemblage Avant bras.SLDASM]
2023-04-13 Départ de démonstration dans l'interface
2023-04-14 plan E des démonstrations manuelle
2023-04-16 modified: Puissance Gant/Programmation/Code_Gant/.pio/build/esp32doit-devkit-v1/idedata.json modified: Puissance Gant/Programmation/Code_Gant/src/main.cpp
2023-04-16 deleted: Puissance Gant/GantUI/.pio/build/esp32doit-devkit-v1/.sconsign39.dblite deleted: Puissance Gant/GantUI/.pio/build/esp32doit-devkit-v1/FrameworkArduino/Esp.cpp.d deleted: Puissance Gant/GantU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
2023-04-16 Update LICENSE.txt
    changer de MIT à CERN-OHL-W
2023-04-17 Déplacer et commenter le code de l'OpenCR
    [5-16_Stainless_Steel_Ball.SLDPRT, 535198.SLDPRT, 545548_hub.SLDASM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]
2023-04-17 modif piece mec
    [Mécanisme poignet 1.sldprt, Mécanisme poignet 2.SLDPRT, XL-430_new.sldasm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]
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2023-04-17 changement nom mec
    [Assemblage_total.sldasm, Avant-Bras.sldprt, Mécanisme_Poignet_1.sldprt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]
